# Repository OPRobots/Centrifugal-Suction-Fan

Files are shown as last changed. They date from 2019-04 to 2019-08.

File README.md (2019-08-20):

# Centrifugal-Suction-Fan
Sistema de succión empleado en #DragonBot y #FujitoraBot
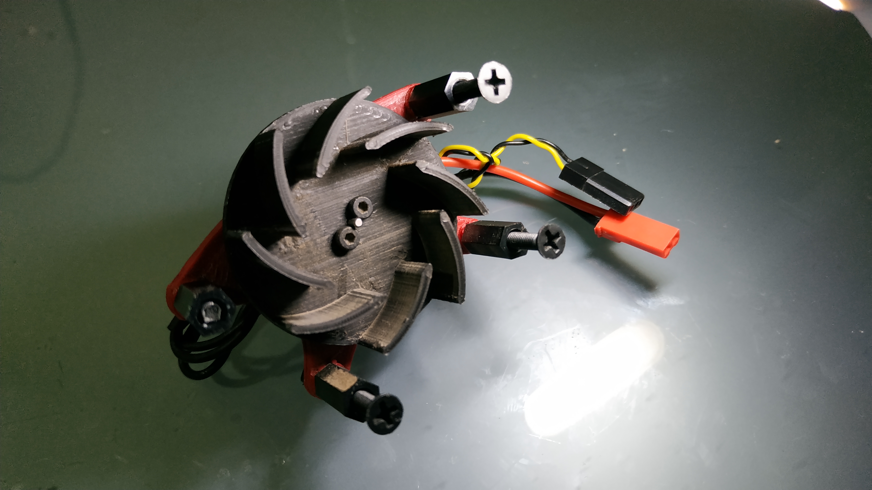
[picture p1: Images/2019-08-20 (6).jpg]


Para la construcción del sistema de succión centrifugo hay dos partes principales, El ventilador, y la falda. Ambos elementos son cruciales para un funcionamiento eficiente.

#VENTILADOR:
A la hora de diseñar el ventilador hay muchos factores a tener en cuenta cuyos parámetros fueron obtenidos en base a prueba y error, sacando algunas conclusiones personales de los resultados, pero sin estar cotejados con ningún software de dinámica de fluidos o alguna fórmula física. Solo daré mi opinión que puede estar acertada o no. Por favor tengan esto en cuenta. 

El objetivo de realizar un ventilador centrifugo es lograr crear una zona de baja presión debajo del robot para que aparezca una fuerza de atracción al suelo debido a la diferencia de presión encima y debajo del robot. Para lograr la mayor efectividad existe una fórmula que dice lo siguiente:

	Qmax = (φ * (R ^ 2) * H * ω) / 2

**φ:** coeficiente de flujo 

**R:** diámetro exterior del ventilador

**H:** altura de las palas del ventilador

**ω:** Ventilador de velocidad angular de rotación

En definitiva, podemos llegar a la conclusión de que lo que más afecta es que cuanto mayor sea el diámetro exterior del ventilador mayor será el "vacío" que generemos debajo del robot. También podemos decrementar la presión haciendo el ventilador más alto o aumentando su velocidad. Pero es menos significativo que aumentar el radio exterior.
En cuanto al resto de parámetros los hemos realizado en función de la experiencia:

- Nº de palas: El número de palas suele estar comprendido entre 6 y 8 en función del tamaño del ventilador, la velocidad de giro y la curvatura de las palas.

- Velocidad de giro: Nosotros usamos un motor Brushless 1404 de 3500-4500kvs esto son entre 28krpms y 36krpms a 2s es común encontrar centrifugas que usan motores coreless que suelen ir a 52krpms a mayor velocidad creemos que es mejor reducir e inclinar las palas para que no ofrezca tanta resistencia

- Angulo de las palas: las palas están giradas respecto al radio de la circunferencia uns 45º con una ligera curvatura en lugar de ser rectas. Esto es porque en el centro del ventilador el motor proporciona más par y puede soportar mayor carga y a medida que se acerca al borde del ventilador el par proporcionado disminuye, por tanto, una curvatura en la pala aumenta la eficiencia. Cuanto mayo par desarrolle tu robot más pronunciada puede ser esta curvatura. Pero también tendrá más carga y afectará en el consumo. Con un par alto también se podría bajar un poco el ángulo de la pala para expulsar más aire. Pero también afectará al consumo. Hay que buscar una relación de compromiso

- Agujero en el robot: El agujero en el chasis del robot no debe abarcar el 100% del diámetro del ventilador, más bien sobre el 60-70% En nuestros robots tenemos un diámetro externo de ventilador de unos 38mm y un agujero de unos 28mm

- Posición del ventilador: El ventilador cebe ir lo más pegado al chasis cuanto sea posible sin que roce contra él. Para minimizar la entrada de aire por el propio agujero. Y para que las palas tengan menos aire que desplazar. Además, la colocación el sistema centrifugo es recomendable que esté centrado en el robot, pero el centro de la presión de "vacío" no estará determinada por la posición del ventilador, sino por el centro del área de la falda. La cual explicamos ahora.

#FALDA:
La falda es sin duda un elemento CLAVE! a la hora de lograr que este sistema sea eficiente, y de lograr gran fuerza de succión. Se encarga de contener la diferencia de presión y evitar que entre aire para que el ventilador trabaje casi sin carga y así reducir significativamente el consumo. La falda es sin lugar a dudas un 80% de la eficiencia del sistema, como mínimo. Para elaborar una buena falda solo hay que tener en cuenta que hay que crear un área lo más estanca posible. Donde entre la menor cantidad de aire, siendo lo ideal que no entre nada de aire, y que el material empleado sea lo suficientemente deslizante para no frenar al robot al rozar contra el suelo mientras corre, y duradero para que no se desgaste por el camino. Os explicamos como la hacemos nosotros:

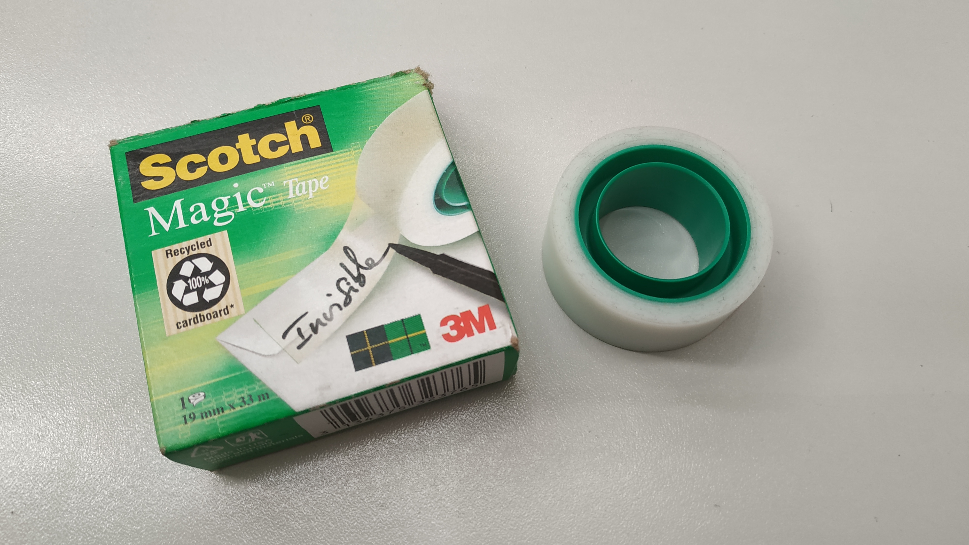
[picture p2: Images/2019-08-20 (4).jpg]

Para crear el área de la falda usamos Scotch magic tape. Es muy deslizante duradero, pega muy bien, y no deja residuos en el robot cuando quitas la falda para poner una nueva.

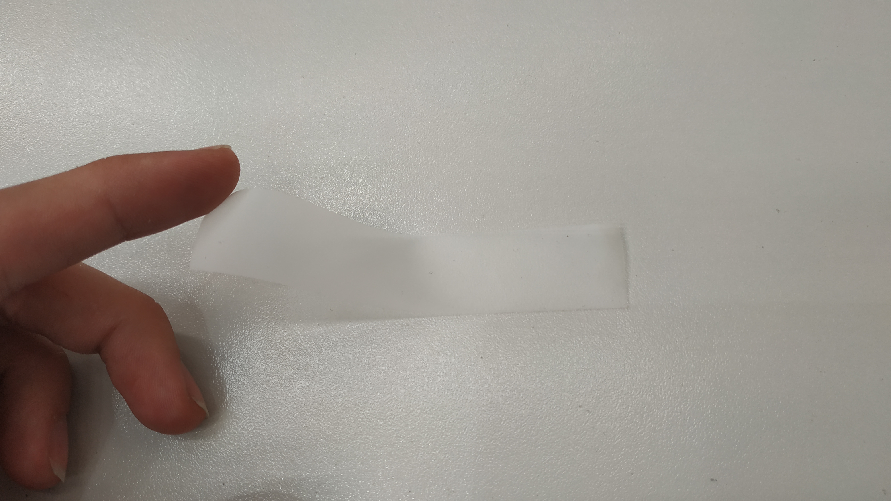
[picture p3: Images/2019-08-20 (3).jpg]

Cortamos una tira de celo de la longitud deseada, y la apoyamos en una mesa con el adhesivo hacia arriba.

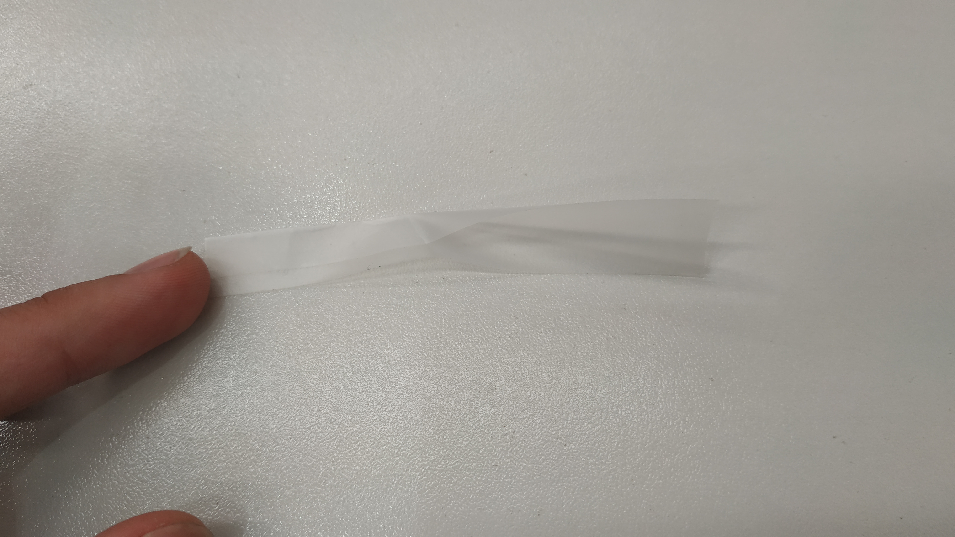
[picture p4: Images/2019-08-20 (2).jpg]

Doblamos el celo sobre sí mismo a lo largo, dejando 4-5mm de adhesivo para poder pegarlo más tarde al robot.

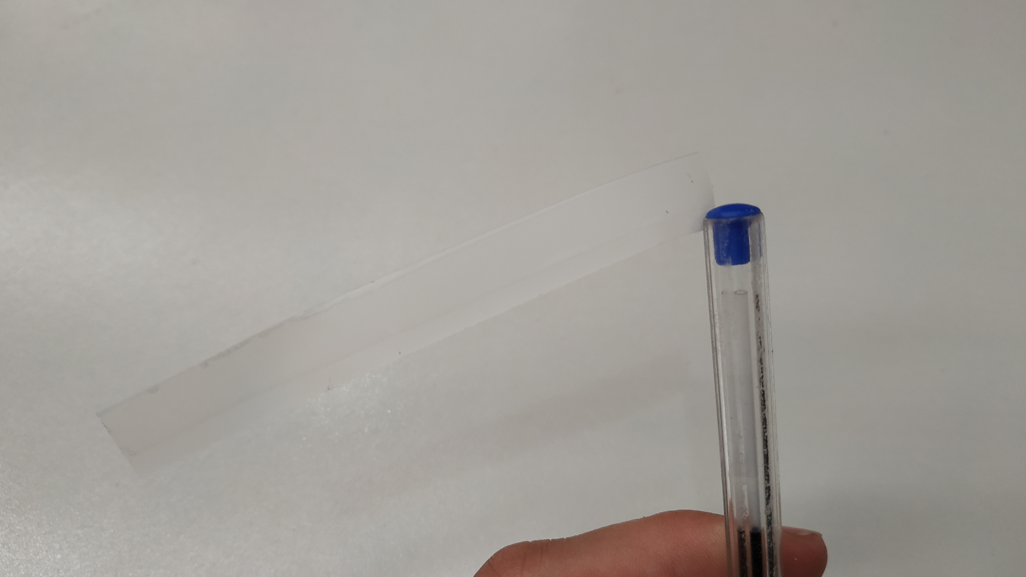
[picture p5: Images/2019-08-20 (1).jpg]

Este sería el resultado final de una de las tiras.

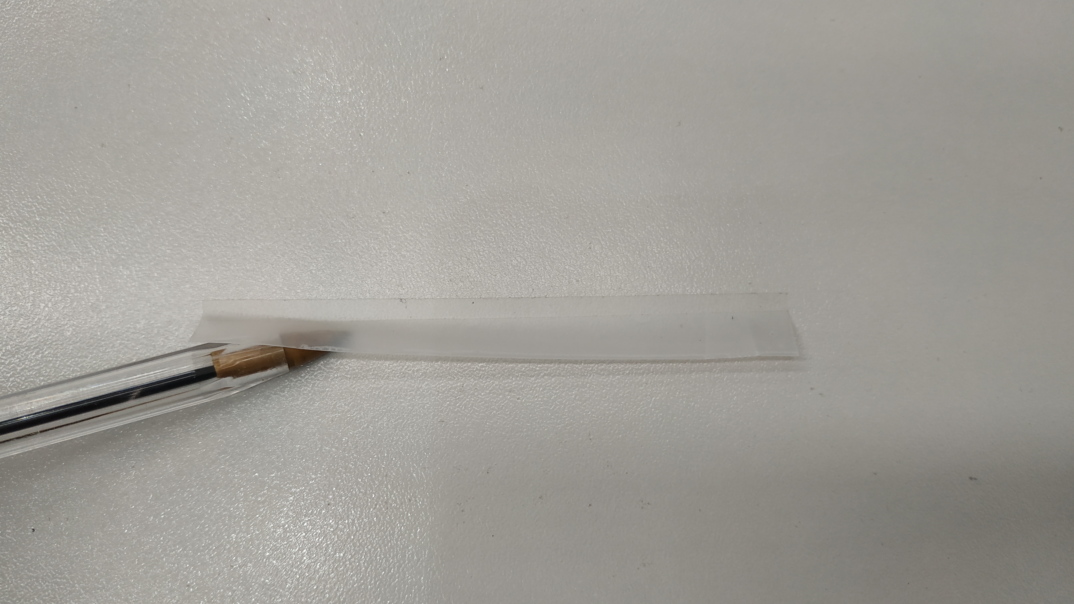
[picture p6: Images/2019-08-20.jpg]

Y así sería como quedaría pegado.

De esta forma creamos unas 5 tiras y las pegamos debajo del robot haciendo un área cerrada, con un pico en la punta para que no se enganche en posibles desniveles que pueda tener la pista, y listo.

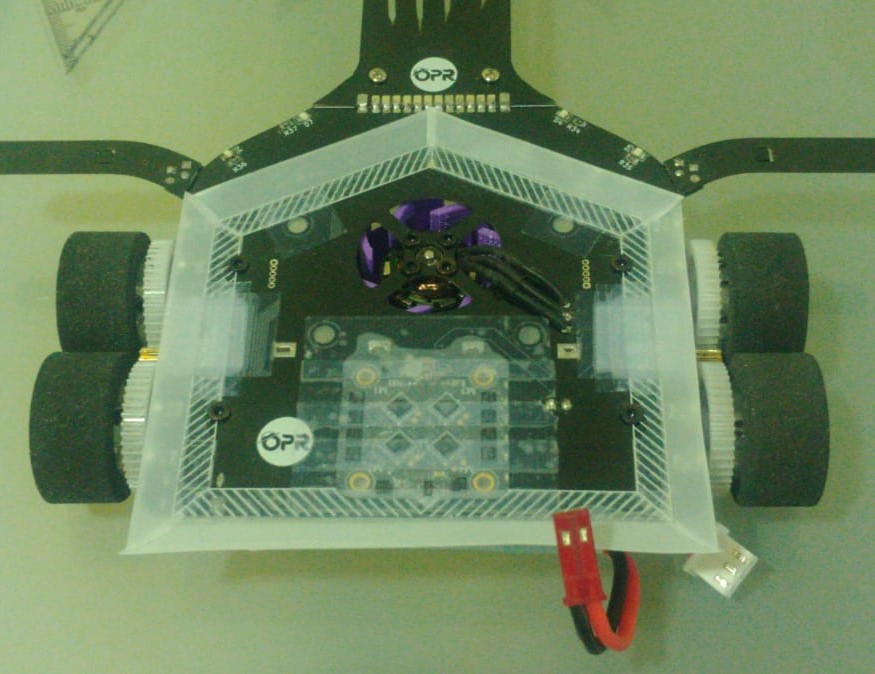
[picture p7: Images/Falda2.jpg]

Este sería el resultado final. También hemos tapado con celo todos los agujeros y posibles huecos por conde podría entrar aire por el propio chasis para evitar romper la estanqueidad. 

Links de referencia:
 - http://hidejr1053.web.fc2.com/vq2.html

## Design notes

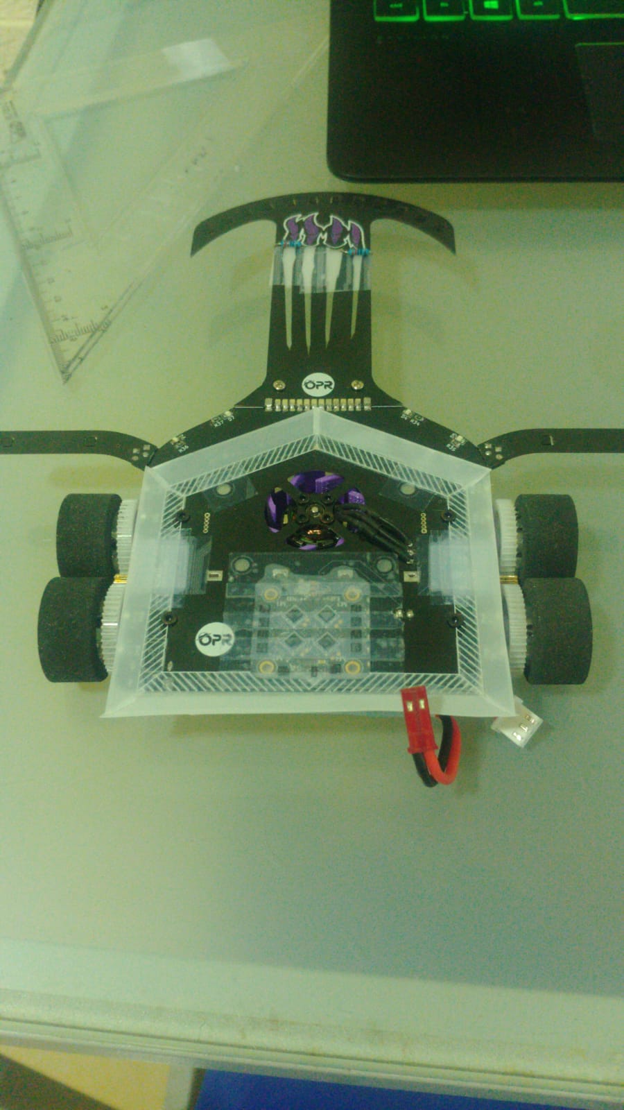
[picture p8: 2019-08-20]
Images/Falda.jpg

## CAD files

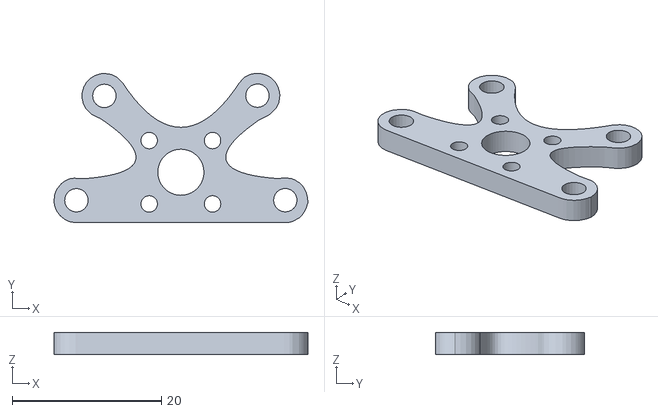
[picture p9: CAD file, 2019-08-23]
stl_files/SoporteVentilador2_modelo2.stl
34.0 x 20.0 x 3.00

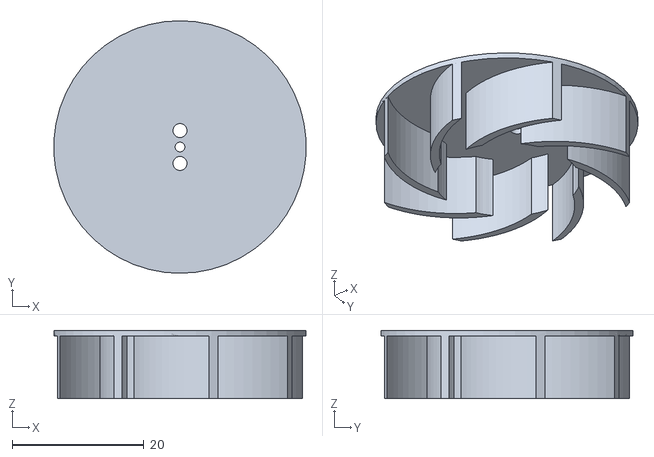
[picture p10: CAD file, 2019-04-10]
stl_files/ventilador.stl
38.3 x 38.4 x 10.4

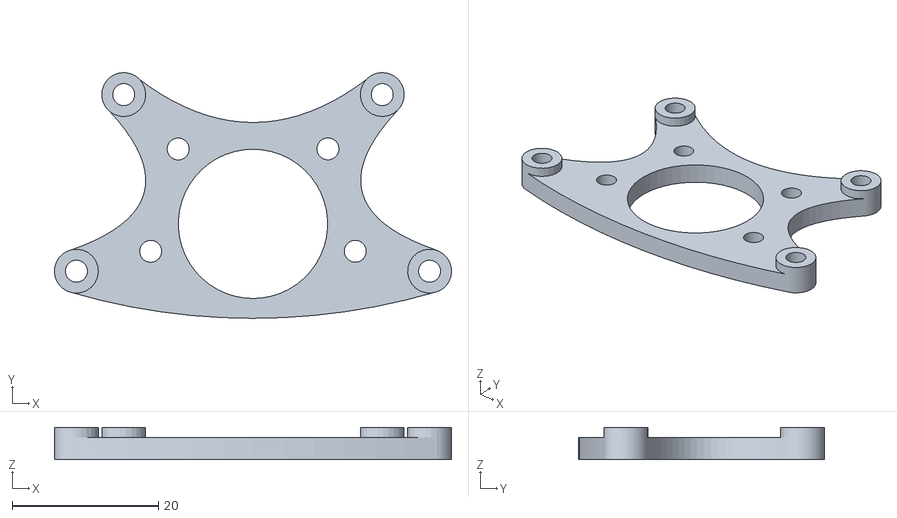
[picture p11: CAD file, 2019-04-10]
stl_files/SoporteVentilador1.stl
54.3 x 33.6 x 4.40

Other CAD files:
stl_files/SoporteVentilador2.stl
